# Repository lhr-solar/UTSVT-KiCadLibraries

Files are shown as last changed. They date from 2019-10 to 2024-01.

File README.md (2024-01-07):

# Common Libraries
This repository contains the footprint and symbol libraries that are used among us, the Longhorn Racing Solar Vehicles Team. 
In order to work on the hardware for our system, please follow the below standard practices when designing a new board.

# Using this Repository
In order to use the files in this repository, you must:
1. Add this repository as a submodule to the PCB repository. It will then show up as a folder within the PCB repository.
2. Create the PCB KiCAD Project and open it in KiCAD.
3. Click on `Preferences` -> `Manage Symbol Libraries` -> `Project Specific Libraries` and add the `.lib` files (within the submodule directory) to the path.
    
    **NOTE**: Ensure all `.lib` files are named `utsvt-name`

# Board Repositories
* All board repositories should contain this repository as a submodule.
* All board repositories should be named Team-BoardName (ex. BPS-LeaderPCB) - all board names should end in PCB
* All board repositories should have zip file of gerbers for the board
* All board repositories should contain pdf with images of board schematic and board layout (with dimensions)
* All board repositories should have `BoardName-backups/*` directory in their `.gitignore` file to ignore all backups generated.
* All board repositories should have README that contains the following information
    * Boards Purpose
    * Mouser link BOM for Board
    * List of components that take up vertical/horizontal volume outside of regular board dimensions (for mechanical purposes)
    * List of LED's on board and what information they provide

# Pull Request Template
The file PULL_REQUEST_TEMPLATE.md should be copied into the main board repository directory. This file creates a checklist of 
things the hardware engineer must complete after opening a PR. After submitting a PR, you must ensure this checklist is completed. Only after
the checklist is completed will a reviewer review your board.

    **NOTE**: After making changes to your board, it is essential that you re-request a review from the reviewers. Otherwise they will not know when
to review your design again. YOU MUST BE PROACTIVE IN YOUR WORK!

When first creating your board repository, and every time the Pull Request Template is updated, you must run the following command
`cp common/PULL_REQUEST_TEMPLATE.md .` to copy the Pull Request Template into the board repository.

# Adding Components to library
1. Add component information to Standardized Mouser Components Excel Sheet (this is so other designs can take this component into consideration if the use is applicable).
    * Be sure to include component name, mouser cart link, and footprint.
2. Open the PCB that you are working on in KiCAD (under its repository)
3. Click on `Symbol Editor`, select a `UTSVT` library to add it to, and click on `Add a New Symbol`.
4. Download component symbol and footprint (or make one yourself using symbol/footprint editor in KiCAD)
    * You may not need to download footprints/symbols for some components. Some footprints/symbols will work for multiple components if they are same package/pinout.
5. If component is large (vertically or horizontally), download 3d model for component.
6. All symbols should have the following information filled out when added:
    * Name
    * Datasheet/Mouser link
    * Footprint Association
7. If adding footprint, click on `Footprint Editor`, select a `UTSVT` folder to add it to.
8. If component takes up vertical or horizontal space (buck converters, connectors, large capacitors, etc.), follow the below steps:
    1. Download footprint and store in the submodule through your PCB repository
    2. Open KiCAD through your project file in your PCB repository. Select `Preferences` -> `Configure File Paths` -> `+` -> and add the following path `$(KIPRJMOD)/common/utsvt3d/`.
    3. Now when adding the 3D Model to the footprint, just select the footprint through the footprint library, click on 3D Models, and add the name of the step file (through one of the folders in `utsvt3d`).
9. After filling out the above information, enter the submodule directory through your PCB repository.
10. There will be changes made to this submodule if everything was done correctly. Now you must commit your changes to a new branch and open a Pull Request.
11. After the Pull Request is merged, update the submodule in your PCB repository through `git submodule update`.

# Standard Constraints for Laying out Board
When manufacturing a PCB, there are constraints that are given to us by the manufacturer based on how precise their manufacturing equipment is. The following are [**JLCPCB Manufacturing Capabilities**](https://jlcpcb.com/capabilities/Capabilities).  
When creating the layout of your board, select
`File` -> `Board Setup` -> `Constraints` and set them to the following values:
* Minimum Clearance (2 layer): .127mm
* Minimum Track Width (2 layer): .127mm
* Minimum Clearance (4 layer): .09mm
* Minimum Track Width (4 layer): .09mm
* Minimum Connection Width: 0mm
* Minimum Annular Width: .13mm
* Minimum Via Diameter (2 layer): .5mm
* Minimum Via Diameter (4 layer): .25mm
* Copper to Hole Clearance: .254mm
* Copper to Edge Clearance: .3mm
* Minimum Through Hole: .3mm
* Hole to Hole Clearance: .5mm
* Minimum Item Clearance: .15mm
* Minimum Text Height: 1mm
* Minimum Text Thickness: .153mm

# Exporting a Board as a 3D Model
Before exporting a board go into the 3D viewer of KiCAD `View` -> `3D Viewer` while in the PCB editor to see what you will be exporting. 
* For mechanical integration, mechanical doesn't need to see every individual component.  If your board doesn't have any smd parts that take up vertical or horizontal space then while in the 3D viewer do `Preferences` -> `Toggle SMD 3D Models` the same applies for any tht component except it's `Preferences` -> `Toggle Through Hole 3D Models`.  
* Go to `File` -> `Export` -> `Step` and select the directory you want to export to and in the `Coordinantes` section make sure `Board Center Origin` is selected.
* Press `Export`.

# Working on a Board
* The first page of the KiCAD schematic should have a version control description of the board that is being worked on. It should list the changes between each version of the board and changes that should be made in future versions of the board.
* When working on a board, the branch name should be the version of the board.
* Versions are updated every time the layout of the board is changed after a fabrication.
* Everyone working on boards should download the Interactive HTML BOM plugin for KiCAD. After laying out the board, an interactive BOM should be generated so soldering the board is easily managed.

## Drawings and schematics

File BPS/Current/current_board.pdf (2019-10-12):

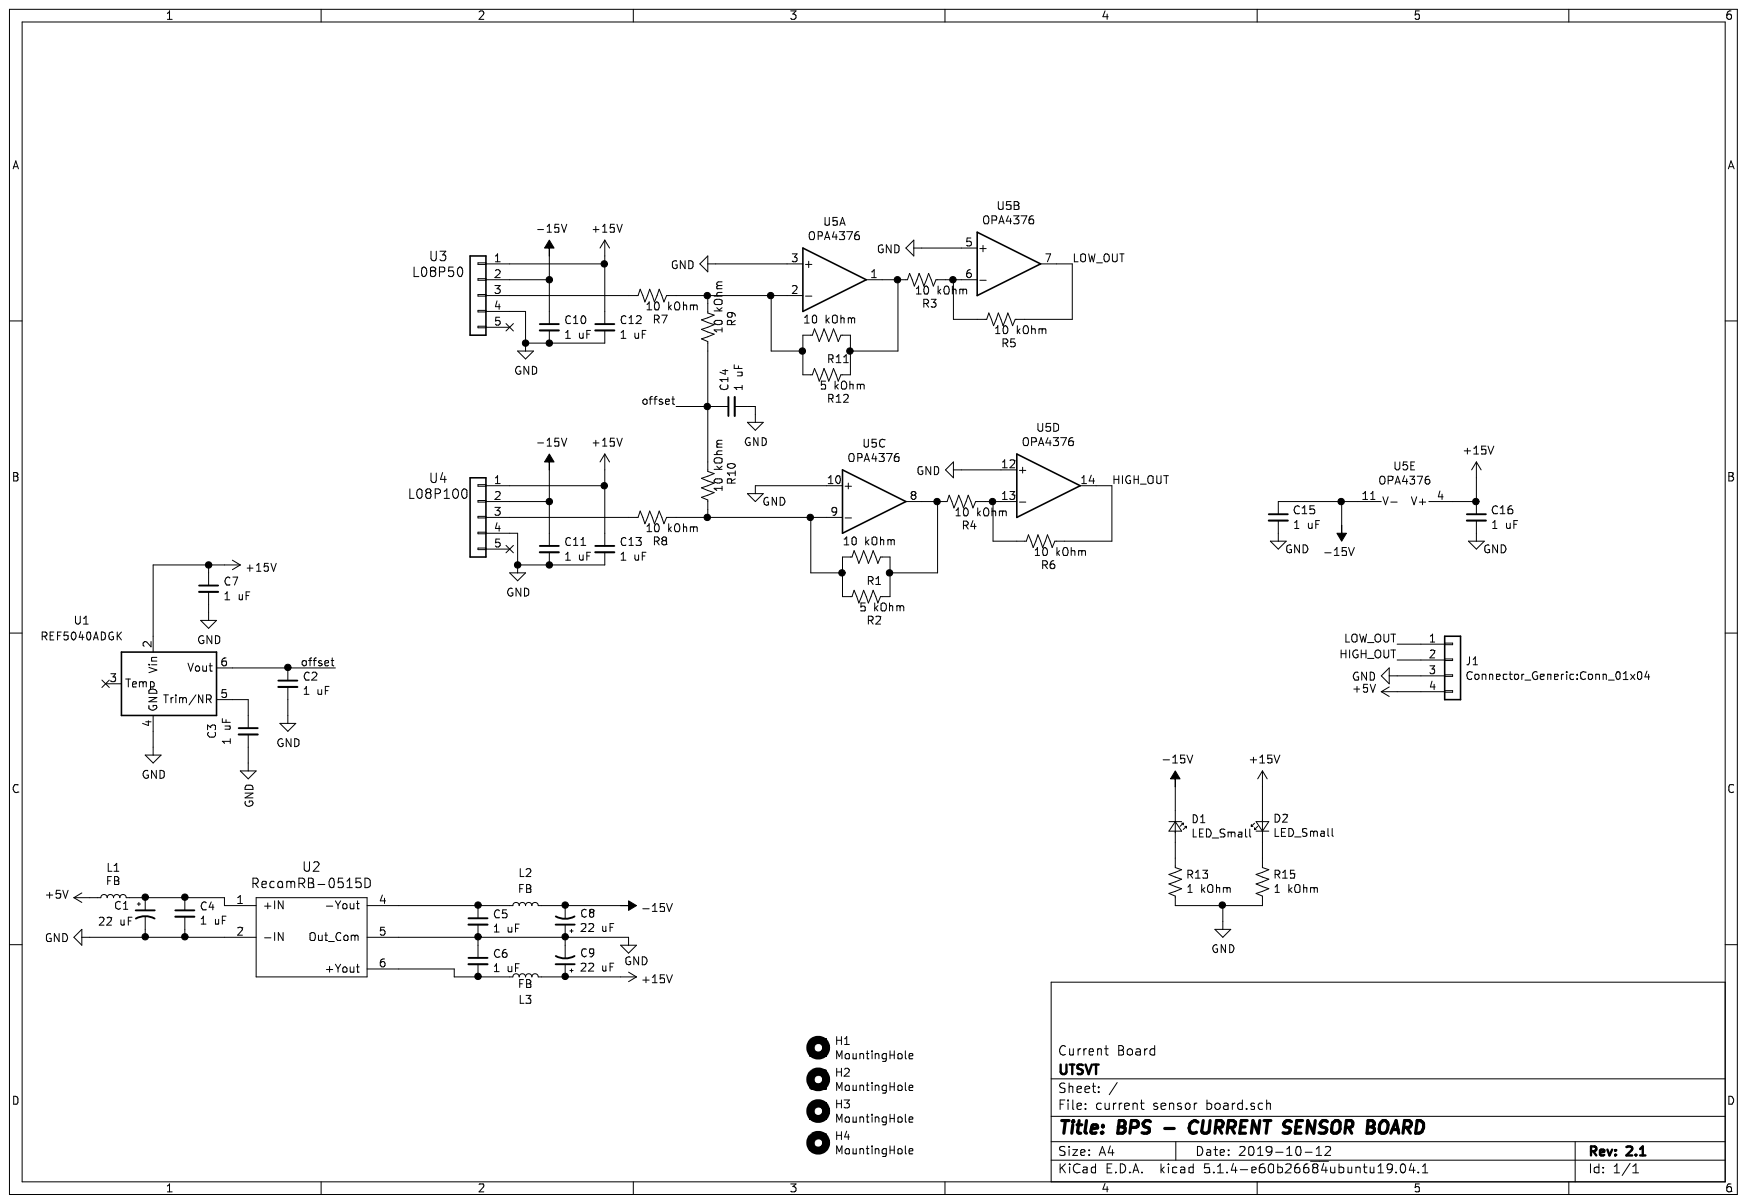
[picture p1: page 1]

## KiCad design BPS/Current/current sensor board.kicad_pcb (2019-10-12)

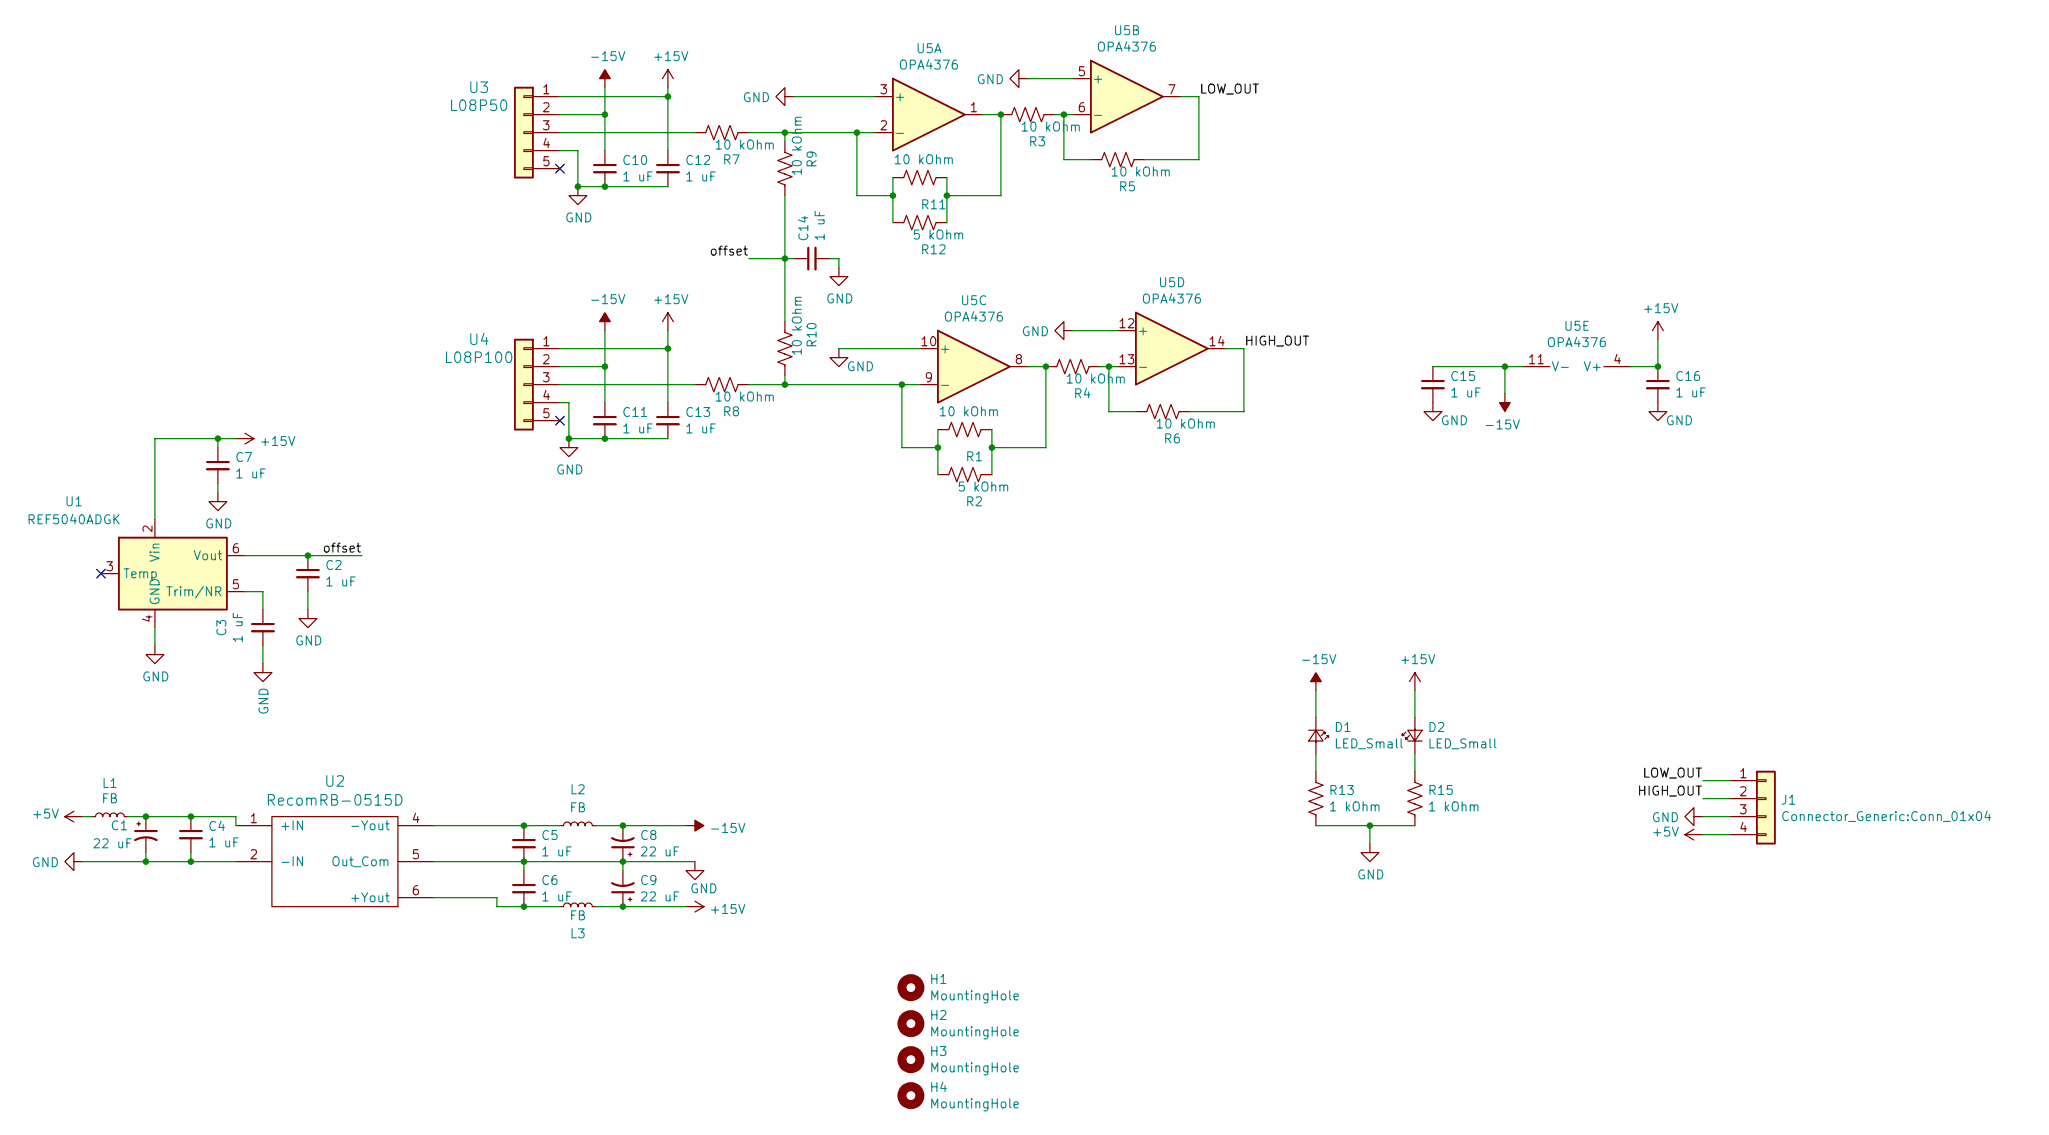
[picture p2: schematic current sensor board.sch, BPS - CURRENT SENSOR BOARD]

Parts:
C1, C8, C9: 22 uF; C_0805_2012Metric
C2, C3, C4, C5, C6, C7, C10, C11, C12, C13, C14, C15, C16: 1 uF; C_0805_2012Metric
D1, D2: LED_Small; LED_0805_2012Metric
H1, H2, H3, H4: MountingHole; MountingHole_3mm
J1: Connector_Generic:Conn_01x04; Molex_Micro-Fit_3.0_43650-0415_1x04_P3.00mm_Vertical
L1, L2, L3: FB; L_1206_3216Metric
R1, R3, R4, R5, R6, R7, R8, R9, R10, R11: 10 kOhm; R_0805_2012Metric
R2, R12: 5 kOhm; R_0805_2012Metric
R13, R15: 1 kOhm; R_0805_2012Metric
U1: REF5040ADGK; MSOP-8_3x3mm_P0.65mm
U2: RecomRB-0515D; SIP-7_19.6x6mm_P2.54mm
U3: L08P50; L08PxxxD15
U4: L08P100; L08PxxxD15
U5: OPA4376; TSSOP-14_4.4x5mm_P0.65mm

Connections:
+5V: J1.4, L1.1
+15V: C7.1, C9.1, C12.1, C13.1, C16.1, D2.2 (A), L3.2, U1.2 (Vin), U3.1, U4.1, U5.4 (V+)
-15V: C8.2, C10.1, C11.1, C15.1, D1.1 (K), L2.2, U3.2, U4.2, U5.11 (V-)
/HIGH_OUT: J1.2, R6.1, U5.14
/LOW_OUT: J1.1, R5.1, U5.7
/offset: C2.1, C14.1, R9.2, R10.1, U1.6 (Vout)
GND: C1.2, C2.2, C3.2, C4.2, C5.2, C6.1, C7.2, C8.1, C9.2, C10.2, C11.2, C12.2, C13.2, C14.2, C15.2, C16.2, J1.3, R13.2, R15.2, U1.4 (GND), U2.2 (-IN), U2.5 (Out_Com), U3.4, U4.4, U5.3 (+), U5.5 (+), U5.10 (+), U5.12 (+)
unnamed: C1.1, C4.1, L1.2, U2.1 (+IN)
unnamed: C3.1, U1.5 (Trim/NR)
unnamed: C5.1, L2.1, U2.4 (-Yout)
unnamed: C6.2, L3.1, U2.6 (+Yout)
unnamed: D1.2 (A), R13.1
unnamed: D2.1 (K), R15.1
unnamed: R1.1, R2.1, R4.2, U5.8
unnamed: R1.2, R2.2, R8.1, R10.2, U5.9 (-)
unnamed: R3.1, R5.2, U5.6 (-)
unnamed: R4.1, R6.2, U5.13 (-)
unnamed: R7.2, U3.3
unnamed: R8.2, U4.3
unnamed: R3.2, R11.1, R12.1, U5.1
unnamed: R7.1, R9.1, R11.2, R12.2, U5.2 (-)

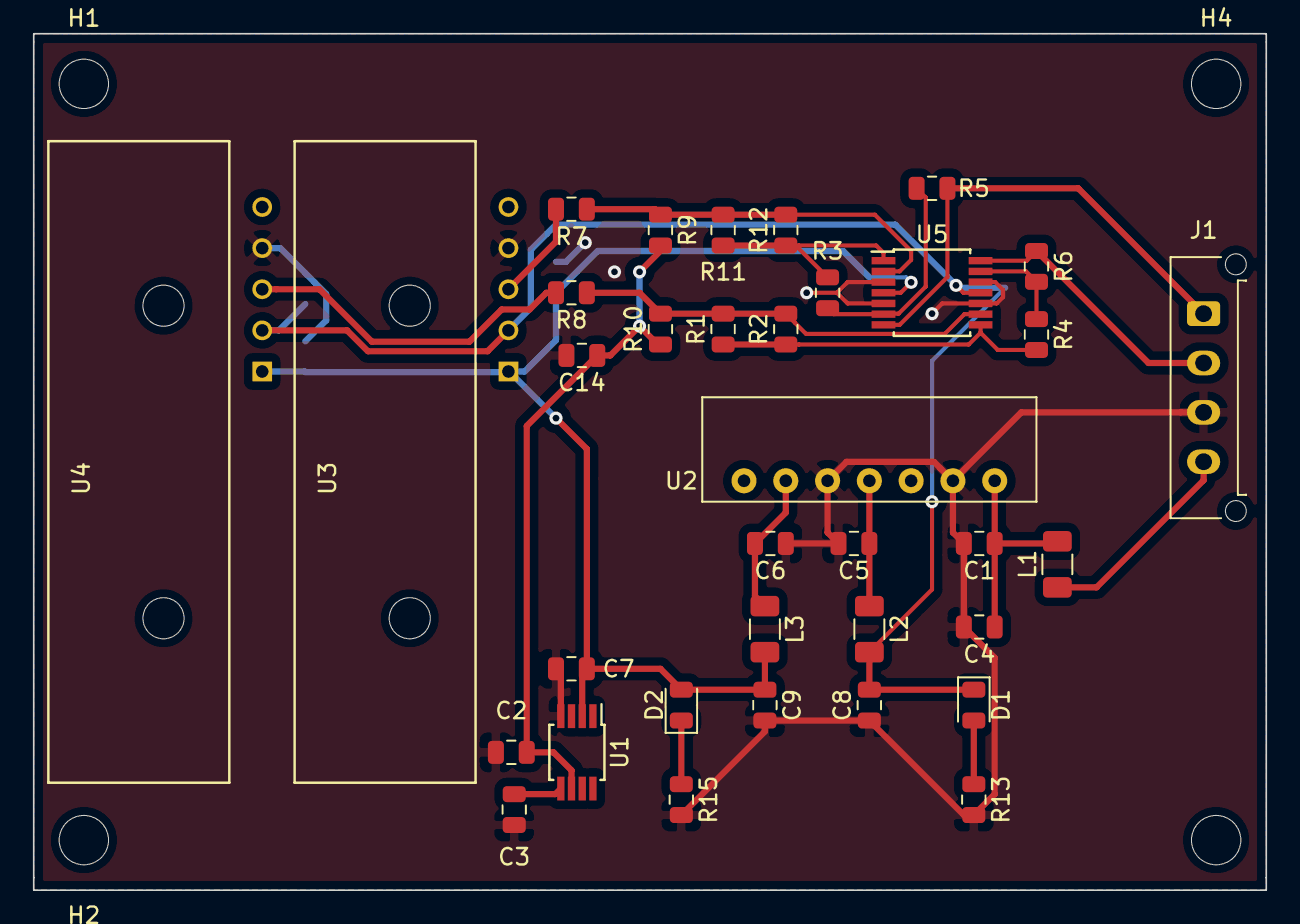
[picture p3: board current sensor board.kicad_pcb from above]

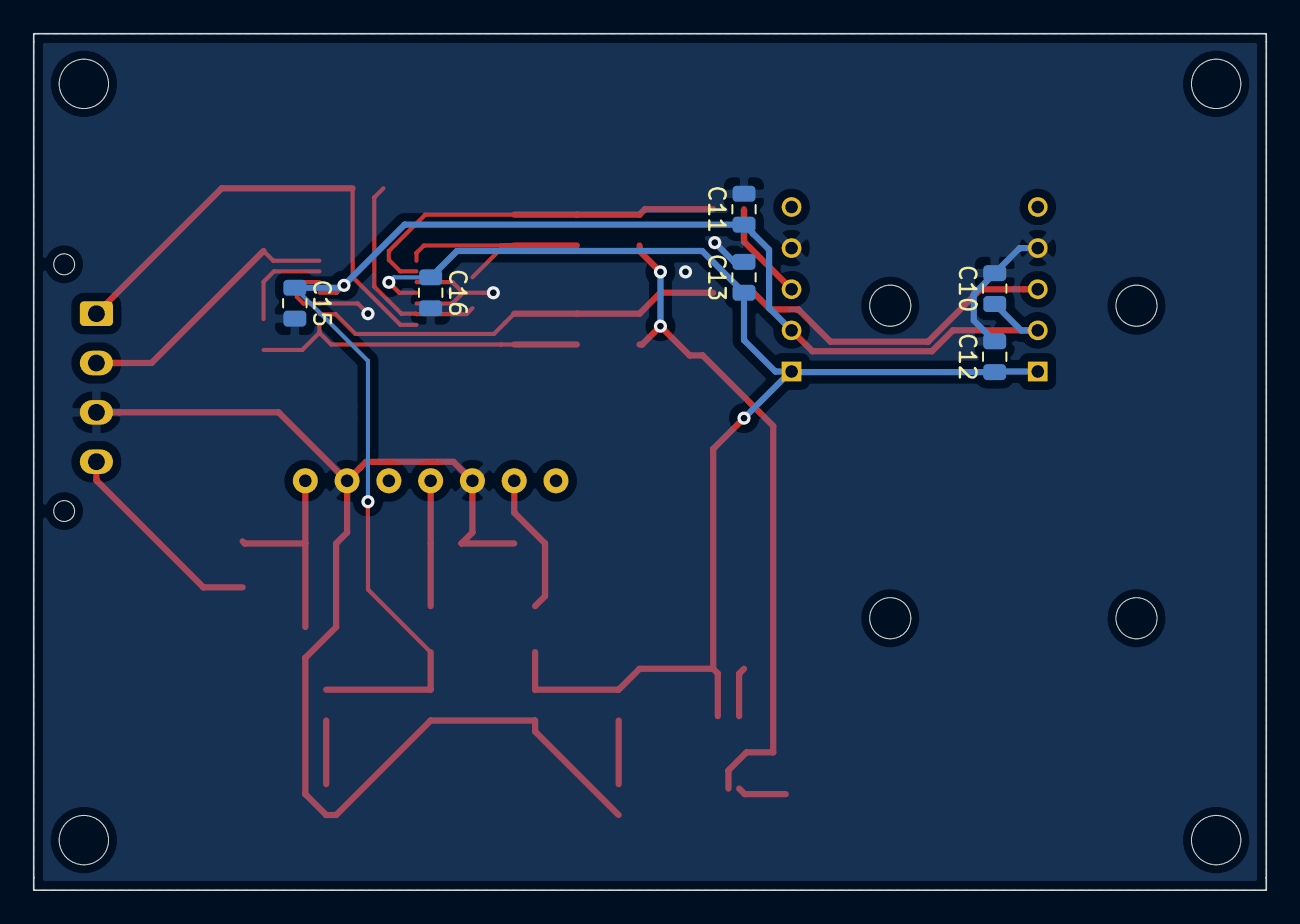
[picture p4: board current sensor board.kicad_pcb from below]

Board: 2 copper layers, 74.9 x 52.1 mm, 45 parts (6 on the bottom side), 21 nets.

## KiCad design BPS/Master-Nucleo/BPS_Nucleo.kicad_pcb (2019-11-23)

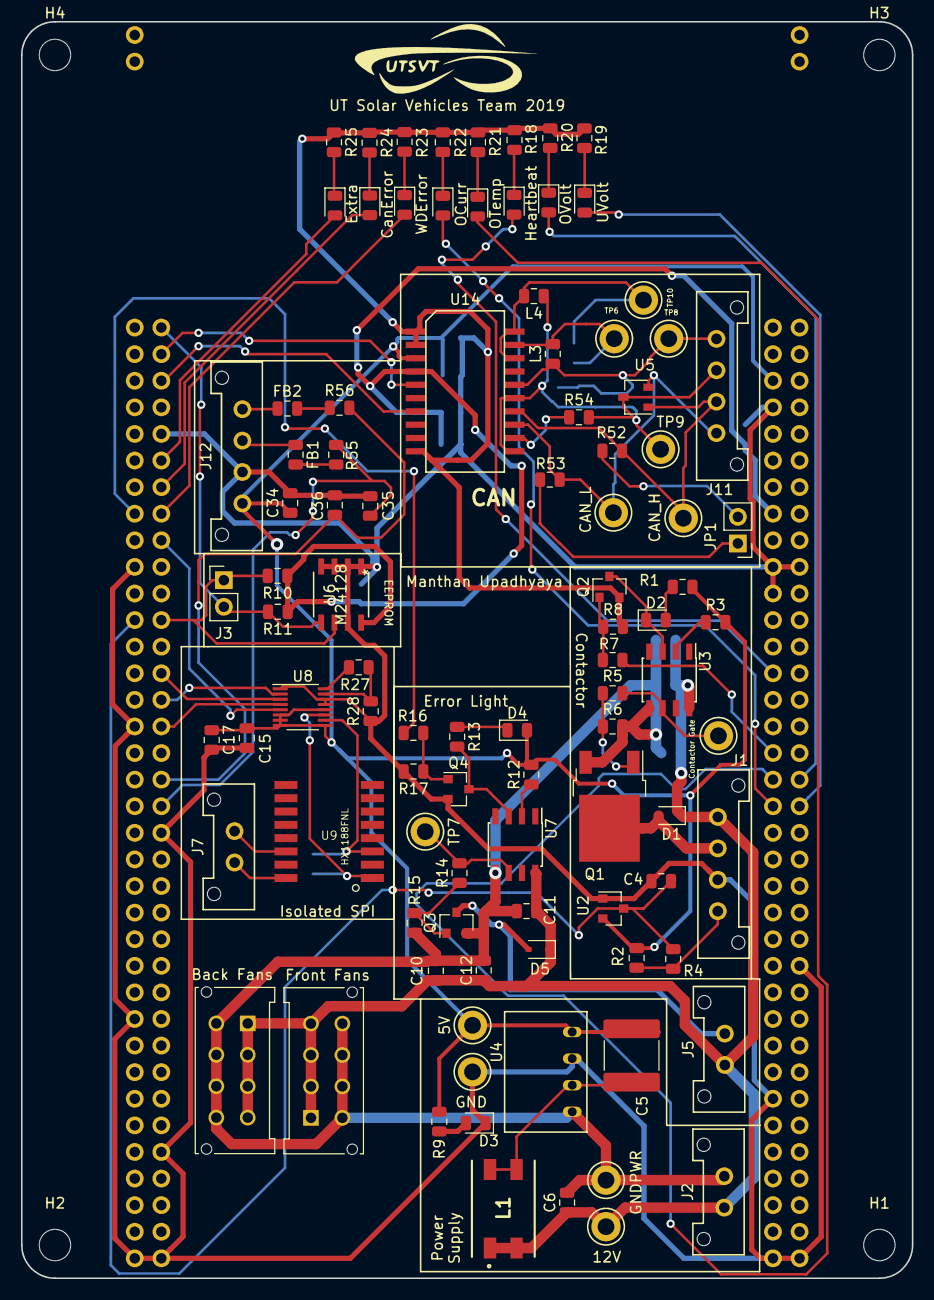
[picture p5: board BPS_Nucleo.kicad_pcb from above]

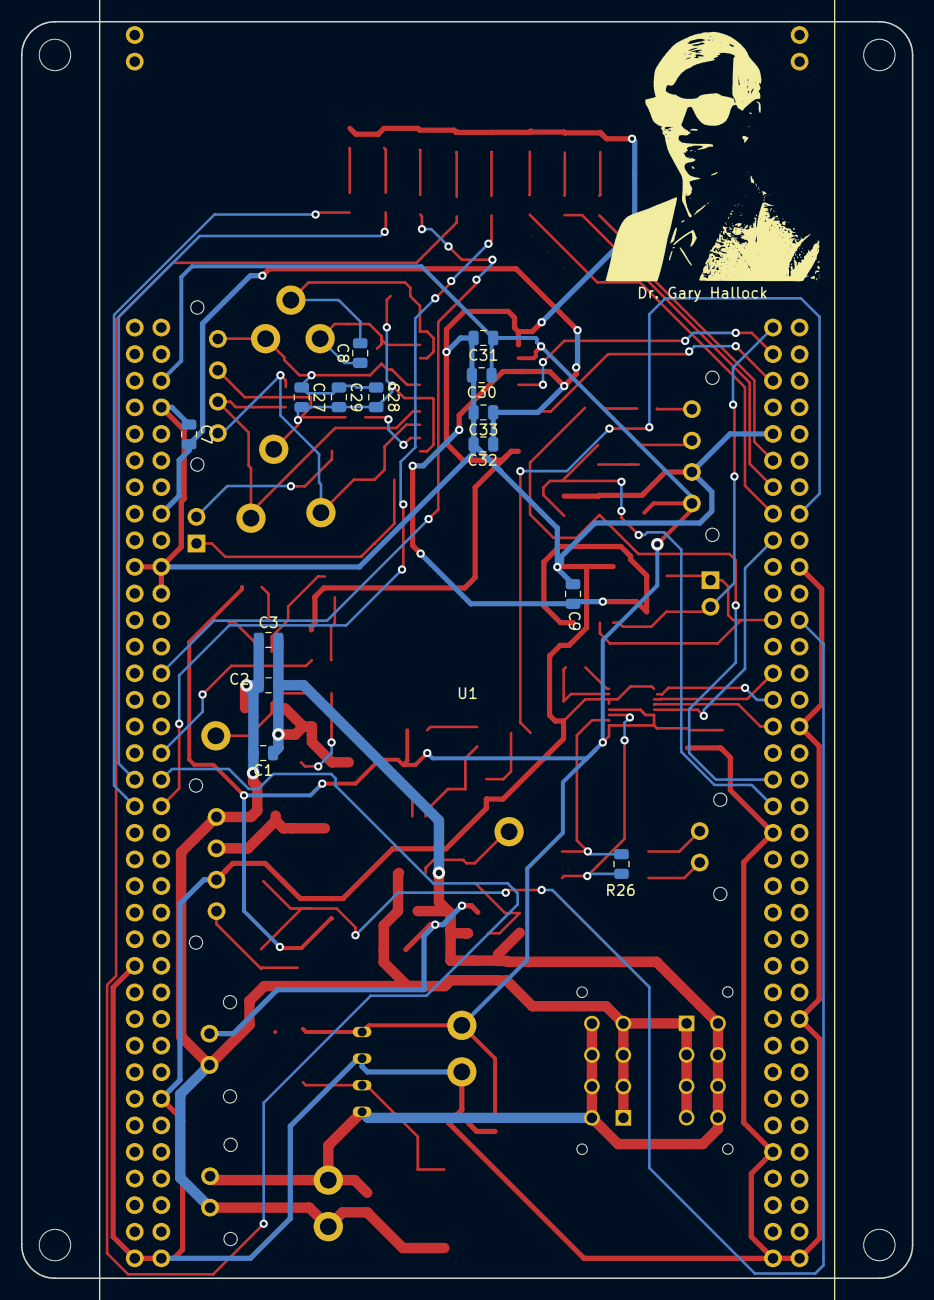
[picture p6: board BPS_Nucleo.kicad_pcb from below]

Board: 2 copper layers, 85.1 x 120.0 mm, 115 parts (15 on the bottom side), 70 nets.

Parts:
5V: +5V_TP; TestPoint_Keystone_5005-5009_Compact
12V: +12V_TP; TestPoint_Keystone_5005-5009_Compact
Back Fans: BackFans; Molex_MicroFit3.0_2x4xP3.00mm_PolarizingPeg_Vertical
C1, C4, C10: 1uF; C_0805_2012Metric
C2, C11, C27, C30: 10uF; C_0805_2012Metric
C3, C7, C9, C12, C15, C17, C28, C31, C32, C34: 0.1uF; C_0805_2012Metric
C5: 470pF; C_2220_5650Metric
C6: 4.7uF; C_0805_2012Metric
C8: 0.22uF; C_0805_2012Metric
C29, C33: 0.01uF; C_0805_2012Metric
C35, C36: 1u; C_0805_2012Metric
CAN_H: CAN_H; TestPoint_Keystone_5005-5009_Compact
CAN_L: CAN_L; TestPoint_Keystone_5005-5009_Compact
CanError: CANError; LED_0805_2012Metric
Contactor Gate: ContactorGate_TP; TestPoint_Keystone_5005-5009_Compact
D1, D5: 1N4148WS; D_SOD-323
D2: ContactorEn; LED_0805_2012Metric
D3: PowerOn; LED_0805_2012Metric
D4: Fault; LED_0805_2012Metric
Extra: Extra; LED_0805_2012Metric
FB1, FB2: 600; L_0805_2012Metric
Front Fans: FrontFans; Molex_MicroFit3.0_2x4xP3.00mm_PolarizingPeg_Vertical
GND: GND_TP; TestPoint_Keystone_5005-5009_Compact
GNDPWR: GNDPWR_TP; TestPoint_Keystone_5005-5009_Compact
H1, H2, H3, H4: MountingHole; MountingHole_3mm
Heartbeat: Heartbeat; LED_0805_2012Metric
J1: ContactorConnector; Molex_MicroFit3.0_1x4xP3.00mm_PolarizingPeg_Vertical
J2: CarPowerConnector; Molex_MicroFit3.0_1x2xP3.00mm_PolarizingPeg_Vertical
J3: Conn_01x03; PinHeader_1x02_P2.54mm_Vertical
J5: ErrorLightConnector; Molex_MicroFit3.0_1x2xP3.00mm_PolarizingPeg_Vertical
J7: VoltageSlaveConnector; Molex_MicroFit3.0_1x2xP3.00mm_PolarizingPeg_Vertical
J11: CAN_Out; Molex_MicroFit3.0_1x4xP3.00mm_PolarizingPeg_Vertical
J12: Conn_01x04; Molex_MicroFit3.0_1x4xP3.00mm_PolarizingPeg_Vertical
JP1: Termination Resistors; PinHeader_1x02_P2.54mm_Vertical
L1: 10uH; SRF0905A
L3, L4: 2kH; L_0805_2012Metric
OCurr: OCurr; LED_0805_2012Metric
OTemp: OTemp; LED_0805_2012Metric
OVolt: OVolt; LED_0805_2012Metric
Q1: VND5N07-E; TO-252-2
Q2, Q3, Q4: NTR4003NT1G; SOT-23
R1, R9: 1.5k; R_0805_2012Metric
R2, R10, R11: 4.7k; R_0805_2012Metric
R3, R12: 470; R_0805_2012Metric
R4: 1k; R_0805_2012Metric
R5, R7, R14, R16, R54: 0; R_0805_2012Metric
R6, R8, R15, R17: 10k; R_0805_2012Metric
R13: 1.6k; R_0805_2012Metric
R18: 680; R_0805_2012Metric
R19, R20, R21, R22, R23, R24, R25: 750; R_0805_2012Metric
R26: 120; R_0805_2012Metric
R27: 806; R_0805_2012Metric
R28: 1.21k; R_0805_2012Metric
R52, R53: 60; R_0805_2012Metric
R55, R56: 220k; R_0805_2012Metric
TP6: CAN_ISO_Vout; TestPoint_Keystone_5005-5009_Compact
TP7: StrobeLightGate_TP; TestPoint_Keystone_5005-5009_Compact
TP8: CAN_ISO_Vin; TestPoint_Keystone_5005-5009_Compact
TP9: CAN_ISO_GndIn; TestPoint_Keystone_5005-5009_Compact
TP10: CAN_ISO_GndOut; TestPoint_Keystone_5005-5009_Compact
U1: NUCLEO144-F412ZG; ST_Morpho_Connector_144_STLink
U2: BAS70-04; SOT-23
U3, U7: SI8261ABC-IS; SOIC-8_3.9x4.9mm_P1.27mm
U4: RI3-1205S; RI3_DC_Converter
U5: CDSOT23-T24CAN; SOT-23W
U6: M24128; M24128-BRMN6P
U8: LTC6820; MSOP-16_3x4mm_P0.5mm
U9: HX1188FNL; HXXXX
U14: ADM3055E; SOIC-20W_7.5x15.4mm_Pitch1.27mm
UVolt: UVolt; LED_0805_2012Metric
WDError: WDError; LED_0805_2012Metric

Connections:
+3V3: C7.2, C9.1, C32.1, C33.1, R10.1, R11.1, U1.16, U6.8, U14.4
+5V: 5V.1, C5.2, C15.1, C17.1, C30.1, C31.1, C34.1, D4.2, J12.1, R1.1, R2.2, R3.2, R9.1, R12.2, U1.6, U2.2, U4.4, U8.6, U8.7, U8.8, U8.9, U8.12, U14.3
+12V: 12V.1, Back Fans.1, Back Fans.2, Back Fans.3, Back Fans.4, C1.2, C2.1, C3.1, C6.1, C10.2, C11.1, C12.1, D1.1, D5.1, Front Fans.1, Front Fans.2, Front Fans.3, Front Fans.4, J1.1, J2.1, J5.1, L1.1, L1.2, U3.8, U7.8
/ADC1_CH2: C36.2, R56.2, U1.107
/ADC1_CH3: C35.2, R55.2, U1.109
/CAN1_RX: U1.75, U14.5
/CAN1_TX: U1.77, U14.7
/CAN/CAN_H: CAN_H.1, J11.3, R52.2, U5.1, U14.14
/CAN/CAN_L: CAN_L.1, J11.4, R53.2, U5.2, U14.13
/CAN/RSlope: R54.1, U14.12
/CAN/TERM_H: JP1.2, R52.1
/CAN/TERM_L: JP1.1, R53.1
/Contactor Driver/CONTACTOR_V-: D1.2, J1.2, Q1.2
/FAULT: R16.2, U1.88
/I2C3_SCL: J3.1, R10.2, U1.95, U6.6
/I2C3_SDA: J3.2, R11.2, U1.73, U6.5
/LTC6811_CS: U1.89, U8.5
/PA5: Extra.2, U1.83
/PA6: CanError.2, U1.85
/PA7: U1.87, WDError.2
/PB0: R7.2, U1.34
/PB1: C4.1, R4.1, U1.96, U2.3
/PC0: OCurr.2, U1.38
/PC1: OTemp.2, U1.36
/PC2: OVolt.2, U1.35
/PC3: U1.37, UVolt.2
/RUN: Heartbeat.2, U1.28
/SPI1_CLK: U1.103, U8.4
/SPI1_MISO: U1.99, U8.3
/SPI1_MOSI: U1.101, U8.2
/SPI/VOLT_IM: R26.1, U8.10, U9.3
/SPI/VOLT_IP: R26.2, U8.11, U9.1
GND: C4.2, C7.1, C9.2, C15.2, C17.2, C30.2, C31.2, C32.2, C33.2, C34.2, C35.1, C36.1, D3.1, GND.1, J1.3, J12.2, Q2.2, Q4.2, R8.2, R17.2, R18.2, R19.2, R20.2, R21.2, R22.2, R23.2, R24.2, R25.2, R28.1, U1.8, U1.19, U1.20, U1.22, U1.49, U1.60, U1.71, U1.72, U1.81, U1.92, U1.104, U1.111, U1.126, U1.135, U1.143, U1.144, U2.1, U4.3, U6.1, U6.2, U6.3, U6.4, U6.7, U8.1, U8.13, U8.14, U14.1, U14.2, U14.10
GNDPWR: Back Fans.5, Back Fans.6, Back Fans.7, Back Fans.8, C1.1, C2.2, C3.2, C6.2, C10.1, C11.2, C12.2, Front Fans.5, Front Fans.6, Front Fans.7, Front Fans.8, GNDPWR.1, J2.2, Q1.3, Q3.2, R6.2, R15.2, U3.5, U4.1, U7.5
unnamed: C5.1, L1.3, L1.4, U4.2
unnamed: C8.1, L3.2, TP6.1, U14.19
unnamed: C8.2, L4.2, TP10.1, U14.18, U14.20
unnamed: C27.1, C28.1, C29.1, J11.1, L3.1, TP8.1, U14.16
unnamed: C27.2, C28.2, C29.2, J11.2, L4.1, R54.2, TP9.1, U5.3, U14.11, U14.15
unnamed: D2.1, Q2.3, U3.3
unnamed: D2.2, R1.2
unnamed: D3.2, R9.2
unnamed: D4.1, R13.1
unnamed: D5.2, J5.2, Q3.3
unnamed: Heartbeat.1, R18.1
unnamed: R19.1, UVolt.1
unnamed: OVolt.1, R20.1
unnamed: OTemp.1, R21.1
unnamed: OCurr.1, R22.1
unnamed: R23.1, WDError.1
unnamed: CanError.1, R24.1
unnamed: Extra.1, R25.1
unnamed: FB1.1, J12.3
unnamed: FB1.2, R55.1
unnamed: FB2.1, J12.4
unnamed: FB2.2, R56.1
unnamed: J1.4, R2.1, R4.2
unnamed: J7.1, U9.16
unnamed: J7.2, U9.14
unnamed: Q1.1, R5.1, R6.1
unnamed: Q2.1, R7.1, R8.1
unnamed: Q3.1, R14.1, R15.1
unnamed: Q4.1, R16.1, R17.1
unnamed: Q4.3, R13.2, U7.3
unnamed: R3.1, U3.2
unnamed: Contactor Gate.1, R5.2, U3.6
unnamed: R12.1, U7.2
unnamed: R14.2, TP7.1, U7.6
unnamed: R27.1, R28.2, U8.15
unnamed: R27.2, U8.16

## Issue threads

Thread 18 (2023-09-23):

Write a KiCAD script to autofill part numbers / mouse part number / mouse link / datasheet for common parts

tiandahuang, 2023-09-23:
some inspiration (this one doesn't work btw):
https://github.com/LonghornRacingElectric/kicad-hax/blob/master/component-autofiller.py

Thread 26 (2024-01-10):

Standardize submodule name

Lakshay983, 2024-01-10:
Some boards use common as the name for this submodule, or they use the name of the repo. Most boards use the repo name instead of common, so we should switch to UTSVT-KiCadLibraries since it's the default when adding the submodule.

What the submodule is called depends on the person making the PCB, but we can be clearer in the instructions on how we want to do things and what things need to be named. Also, some internal directories are used in the symbols like 3D models, so the names need to be standardized.

Fixing this is gonna involve:

- Updating readme to use UTSVT-KiCadLibraries instead of common
- Ctrl-f through the repo and replacing instances of common with UTSVT-KiCadLibraries

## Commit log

2019-10-12 Refactor current folders and remake current board
    [BPSCurrent.kicad_pcb, BPSCurrent.sch, current sensor board V2.kicad_pcb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]
2019-10-12 Add a pdf of the schematic
2019-11-08 Connected all PCB components. Space in middle cannot be utilized. Distance between traces and copper must be less than .127mm or 5 mils according to manufacturer capabilities.
    [BPS-Nucleo.kicad_pcb, BPS-Nucleo.sch, CAN.sch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]
2019-11-09 Before, the components were divided between left and right. Now, they are between the top and right and all connectors are towards the edge.
    [BPS-Nucleo.kicad_pcb, BPS-Nucleo.sch, CAN.sch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]
2019-11-09 Fixed a few connections I didn't notice earlier.
    [BPS-Nucleo.kicad_pcb, BPS-Nucleo.sch, CAN.sch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]
2019-11-16 Before, components were outside board. Moved components to inside of board so usb port is unobstructed. Distance between copper and traces should be 5 mils.
    [BPS_Nucleo.kicad_pcb, SPI.sch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]
2019-11-16 Added silkscreens to certain diodes and testpoints
    [BPS_Nucleo.kicad_pcb]
2019-11-17 Increased area of PCB to include upper components. Added silkscreen of Dr. Hallock.
    [BPS_Nucleo.kicad_pcb]
2019-11-19 Decreased length of PCB on top, left, and bottom and spaced out some resistors in the EEPROM.
    [BPS_Nucleo.kicad_pcb]
2019-11-23 Added mounting holes and footprints. Increased track length of 5v from .25 to .38.
    [BPS_Nucleo-B_Cu.gbr, BPS_Nucleo-B_Mask.gbr, BPS_Nucleo-B_Paste.gbr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]
2020-08-02 Set up the common libaries repository
    [BOM.csv, BPS-Nucleo.kicad_pcb, BPS-Nucleo.sch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]
2020-09-01 Adds power footprint library
2020-09-12 Adds footprints and symbols for the controls leader board
2020-09-19 Add GPS unit footprint
2020-10-10 Assign 3D models to molex connectors
2020-10-24 Add more 3D models for connectors
2020-10-29 Add 3d models relevant to the telemetry board.
2020-12-05 Add more components for the battery secondary
2020-12-05 Add more components for the battery primary
2020-12-18 Banana jack connector
2020-12-20 Adds opamp and dc-dc converter for supplemental monitoring board
2021-01-06 Adds DC-DC converters from BPS Test Board
2021-01-23 Added HX1188FNL chip, 2222 5750 Metric capacitor (2.6mm in height), and 3 hole horizontal connector
2021-01-23 Adds RSD-150 and 2 pin molex connector
2021-01-25 added controls leader board models
2021-11-06 New ADC
2021-12-24 Fix power regulators
2022-09-24 new footprint for Vishay shunt resistor and DPST switch
2022-09-24 Adds switch
2022-09-24 Adds new switch
2022-09-24 New SP3T Footprint
2022-10-01 Added new component footprints for BPS scrutineering board
2022-10-15 added switch
2023-05-04 Added more procedures for footprints
2023-05-06 Updates symbols for Kicad 7
2023-05-22 Support for Controls Simboard
    Added 3D Models and updated footprints for parts used in Control Simboard
    [Molex_Micro-Fit_430450612.stp, Molex_Micro-Fit_430451412.stp, Molex_Micro-Fit_436500415.stp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]
2023-05-22 Removed unnecessary files
    [Molex_Micro-Fit_430450612.stp, Molex_Micro-Fit_430451412.stp, Molex_Micro-Fit_436500415.stp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]
2023-07-18 added instructions on how to export boards as 3D models
2023-08-08 Bps minion standardization (#14)
    * Added 3D models
    * Moved connector 3d model to utsvt3d
2023-08-08 Telemetry primary standardization (#13)
    * lan chip 3d model
    * 3d model linking
    * further footprint/model linking
    * more models
    * footprint margins and proper references
    * remove schematic specific properties
    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
2023-08-09 Fixed Power Regulator Symbols/Footprints
2023-09-13 Peripheral som changes (#16)
    * add D5V0P4UR6SO-7
    * Added SOM connector
    * Cleaned up connector footprint
    * Added connector 3D model
    * new molex connector footprint
    * Added 3D models for connectors and chips
    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
2023-09-21 Added BPS Minion Shield Connector (#12)
    * Added BPS Minion Shield Connector
    * move reference
    * Added ref to footprint
    * Added datasheet, added connector silkscreen, and extended keepout layer
    ---------
2023-10-08 Peripheral som symbol (#19)
    * added peripheralsom footprint
    * Added part number to PeripheralSOM_Connector
    * Added 3D model of PeripheralSOM
2023-11-11 connector footprints (#21)
    * Banana Plug Horizontal Connector
    * Battery Holder Footprints
    * Male and Female connectors
2024-03-25 added footprints and 3d models for DC-DC Fuse PCB(#28)
2024-07-27 Merge SOM components to master (#22)
    * Added DaughterBoard Connector
    * Added Fan Controller IC Symbol
    * Changed Daughter SOM Connector to have Daughter Connector
    * Added 3D model for Daugter Connector
    * added new chip
    * Updated symbols
    * 7 segment
    * oops
    * f
    * asdf
    * (￣y▽￣)╭ Ohohoho.....
    * f
    * added LeaderSOM 3D files
    * added proper LED display 3D model
    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
2024-09-29 Added Contactor Flyback Schottky Diode Footprint (#30)
2024-10-12 Psom symbol (#31)
    * started psom symbol (no footprint)
    * yipee
    * psom footprint
    * changed edgecut to user.drawings
    * moved stuff around
    * fixed 3d model path
2024-10-12 added 16 channel adc/mux, revised psom symbol (#33)
2024-10-18 Add symbol for Peripheral CAN connector (#35)
    * symbol for Peripheral CAN connector
    * add part number
2024-11-19 add symbol for PMV35EPE mosfet

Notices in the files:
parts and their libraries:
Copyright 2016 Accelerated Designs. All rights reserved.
